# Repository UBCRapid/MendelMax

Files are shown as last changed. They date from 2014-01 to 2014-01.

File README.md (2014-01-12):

UBC Rapid
=========

MendelMax Printer
-----------------

Our newest printer, being built following the 1.5+ [MendelMax](http://mendelmax.com/tikiwiki/tiki-index.php?page=MendelMax) design.

### Current Objectives

(And feel free to add in your own)

* Sourcing parts and beginning construction.
* Printing parts (finished, except for extruder)
* Deciding on a classy name for the new member of our printer family. ("Maxwell" ?)

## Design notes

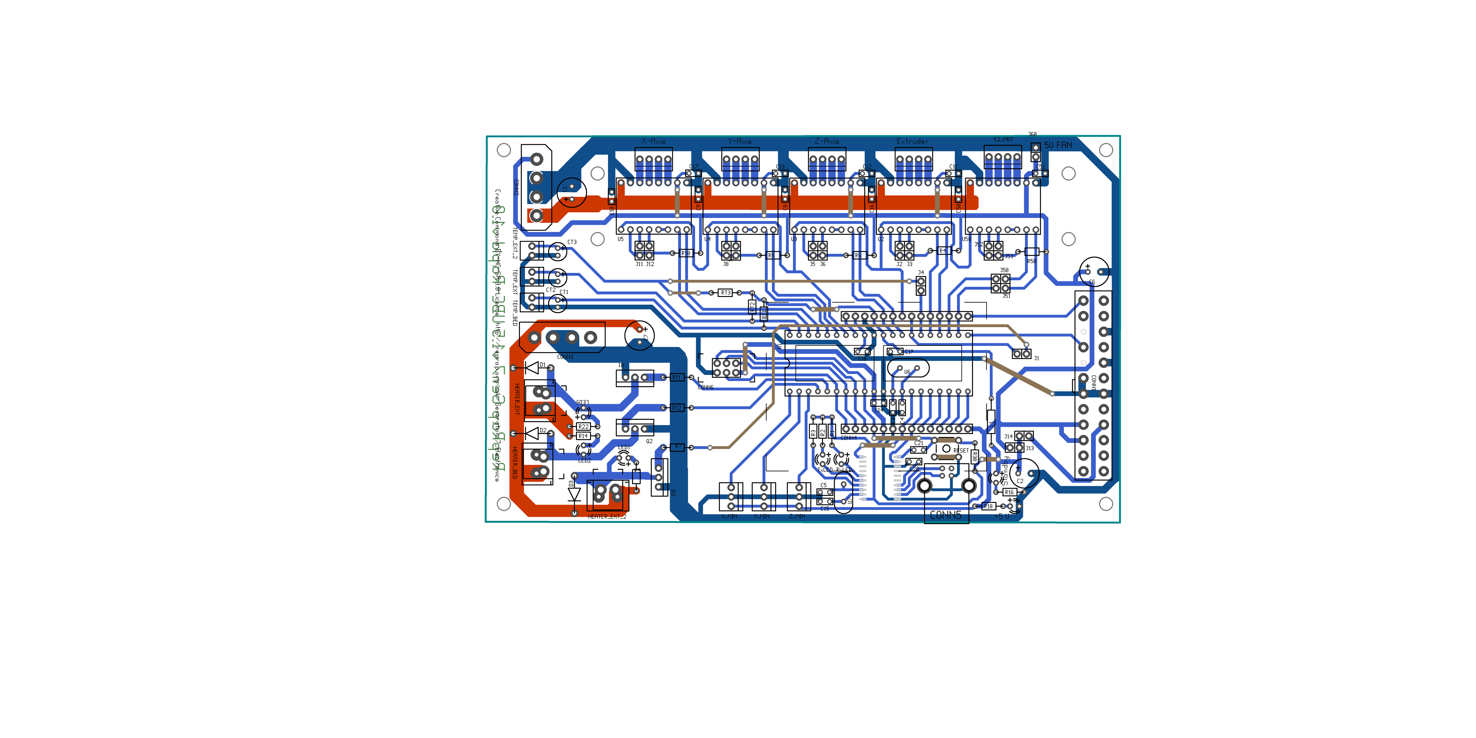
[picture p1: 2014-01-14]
Gen7Respin-Steve/Gen7Board-AVR.png

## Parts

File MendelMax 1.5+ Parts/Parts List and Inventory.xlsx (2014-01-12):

O=ordering
H=Have | MendelMax V1.5+ |  | REVISED 8/31/12 by papabur |  | MendelMax V1.5+ |  | 7/9/2012 (revised 7/9/12 by MP)
❑=not have | Full Kit Packing List |  |  |  | Hardware Kit
nn=not needed
 | Item | Qty. | Used For |  | Item | Qty. | Used For
❑ | Extrusions | 1 set |  | ❑ | Extrusions | 1 set
❑ | 420mm extrusions – Drilled | 2 | Top horizontal bars | ❑ | 420mm extrusions | 2 | Top horizontal bars
❑ | 420mm extrusions | 5 | Lower Y extrusions | ❑ | 420mm extrusions | 5 | Lower Y extrusions + Y Axis Rail Mount
❑ | 340mm Extrusions – Tapped | 4 | Diagonals | ❑ | 340mm Extrusions | 4 | Diagonals
❑ | 300mm extrusions – Tapped | 4 | Lower X extrusions | ❑ | 300mm extrusions | 4 | Lower X extrusions
❑ | Y-Axis Linear Rail and Carriage | 1 set | Y axis | ❑ | Y-Axis Linear Rail and Carriage | 1 set
❑ | Shaft Tube | 1 set |  | ❑ | Shaft Tube | 1 set
H? | M8 Precision Linear Shafting – 445mm | 2 | X axis | ❑ | M8 Precision Linear Shafting – 445mm | 2 | X axis
H? | M10 Precision Linear Shafting – 405mm | 2 | Z axis | ❑ | M10 Precision Linear Shafting – 405mm | 2 | Z axis
❑ | Leadscrews (PBC) | 2 | Z axis | ❑ | Acme Leadscrews | 2 | Z axis
❑ | Electronics | 1 set |  |  | Table Acc.
nn | LED Frame Lights | 2 | wrapped w/ table | ❑ | Borosilicate Glass Table | 1 | Print table
❑ | 24V Kapton Heater | 1 | Insulating bed heater (w/ table) | ❑ | G10 Plate | 1 | Print table lower frame
H | 24V Power Supply | 1 |  | ❑ | PET Film Bed Sheets | 2 | Optional print surface
H | Nema17 Stepper Motor | 4
H | 24V > 12V step down converter | 1 |  | ❑ | Electronics | 1 set
H | USB Cable |  |  | ❑ | LED Frame Lights (5 sections)(w/ table Acc.) | 2
 |  |  |  | ❑ | Silicone Heater (Voltage ______) | 1
❑ | RAMPS Electronics Box | 1 |  | ❑ | SSR (only with 110v or 240v beds!!!) | 1 | (AC Heaters only)
H | Arduino Mega | 1
nn | Endstop Kit | 1 |  | ❑ | Assembly tools | 1 set
H | Pololu Module | 4 |  | ❑ | 1.5mm Allen Key | 1
 |  |  |  | ❑ | 2mm Allen Key | 1
❑ | Assembly tools | 1 set |  | ❑ | 2.5mm Allen Key | 1
H | 1.5 Allen Key | 1 | ( All allen keys are in H.W. Bag) | ❑ | 3mm Allen Key | 1
H | 2mm Allen Key | 1 |  | ❑ | 3.5mm Allen Key | 1
H | 2.5mm Allen Key | 1 |  | ❑ | 4mm Allen Key | 1
H | 3mm Allen Key | 1 |  | ❑ | 6mm Allen Key | 1
H | 3.5mm Allen Key | 1
H | 4mm Allen Key | 1
H | 6mm Allen Key | 1 |  |  | Anti-Bind X axis bushings (in H.W. Bag)
H | Digital Caliper | 1 |  | ❑ | 8mm self-aligning bronze bushings | 4
H | Small Files | 1
H | Large File | 1 |  | ❑ | SSR Hardware Bag (For AC bead heaters only) | 1 set | (See bag label for contents)
H | Pololu Adjustment Tool | 1 | (w/ RAMPs Electronics Box)
H | Square | 1 |  | ❑ | Hardware Bag | 1 set | (See Bag Label for contents)
H | Zip-ties | 10 |  | ❑ | PBC Nuts(in H.W. Bag) | 2
❑ | Plastic Parts | 1 set |  | ❑ | Y Axis Rail Bag (HW bag) | 1 Set | (See Bag Label for contents)
❑ | X Idler End | 1
❑ | X Motor End | 1 |  | ❑ | Y Axis Mounting Bag (HW bag) | 1 Set | (See Bag Label for contents)
❑ | X Carriage Supaflat | 1
❑ | X Carriage Bushing Mounts | 4 |  | ❑ | Bed Thermistor Connector Bag (24V Bed Heaters only) | 1 Set | (See Bag Label for contents)
❑ | X Carriage Belt Clamps | 2
❑ | Y motor Mount | 1 |  |  | Thermistor Bag (Optional)(HW bag) | 1 set | (See Bag Label for contents)
❑ | Y Axis Belt Tensioner | 1
❑ | Y Carriage Belt Bracket | 1 |  |  | Wade's Extruder Bag (Optional)(HW Bag) | 1 set | (See Bag Label for contents)
❑ | Z Motor Mounts | 2
❑ | Z Lower Mount | 2 |  |  | make sure to include a Lead Nut Adapter bag
❑ | Z Rod Clamp | 4 |  |  | with Hardware Kit orders since these people
❑ | Spool Holder Bracket | 2 |  |  | most likely have the old style x-ends!!
❑ | Left Vertex Corner | 2
❑ | Right Vertex Corner | 2 |  |  | -T.S. revised 8/21/12
❑ | Left Vertex Cover | 2
❑ | Right Vertex Cover | 2
❑ | Upper Reinforcing Bracket | 3
❑ | RAMPs Mounting Bracket | 1
 | Table Accesories
? | Borosilicate Glass Table | 1 | Print Surface
? | G-10 Carbon Bed Sheet | 1
H | PET Film Bed Sheets | 2
❑ | Kapton Tape Roll | 1
❑ | 1LB Filament - ❑ ABS , ❑ PLA | 1
❑ | Hardware Bag | 1 set | (See bag label for contents)
 | PBC Nuts(in H.W. Bag) | 2
❑ | Wire Harness and PSU Mount Bag | 1 set | (See bag label for contents)
❑ | Micro Extruder Bag | 1 set | (See bag label for contents)
❑ | Y Axis Rail Bag (in H.W. Bag) | 1 Set | (See bag label for contents)
❑ | Y Axis Mounting Bag (in H.W. Bag) | 1 Set | (See bag label for contents)
❑ | Bed Thermistor Bag (in H.W. Bag) | 1 | (See bag label for contents)

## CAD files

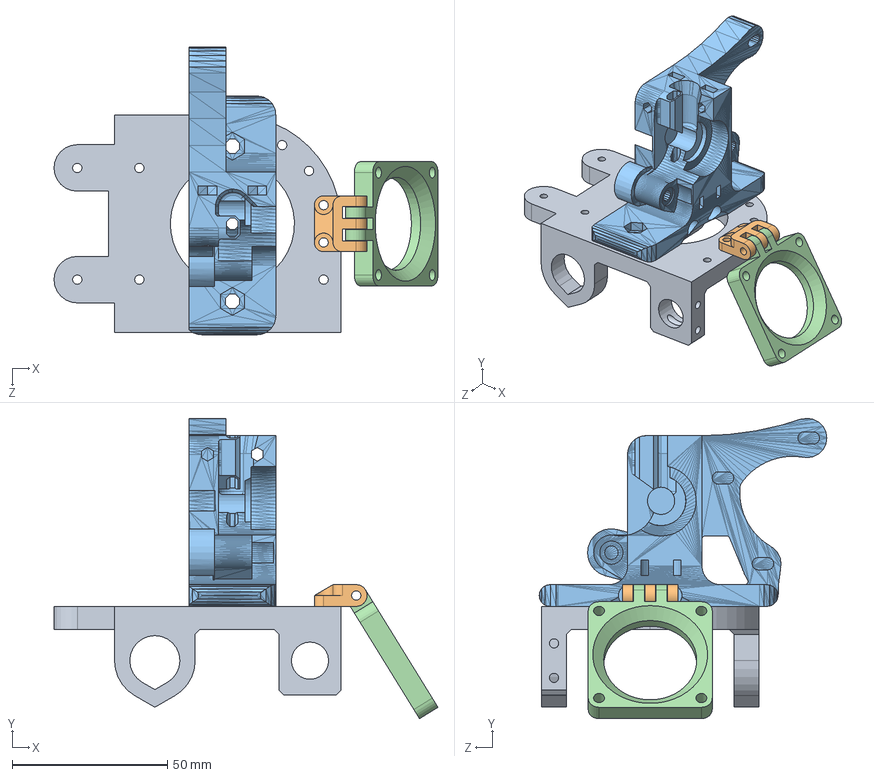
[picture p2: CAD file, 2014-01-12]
MendelMax 1.5+ Parts/Original Parts/Rough XCarriange Assembly.SLDASM
123.7 x 96.8 x 92.7 mm
Specialized X Carriage
Fan Mount 2
Toms_guided_greg
Fan Shroud

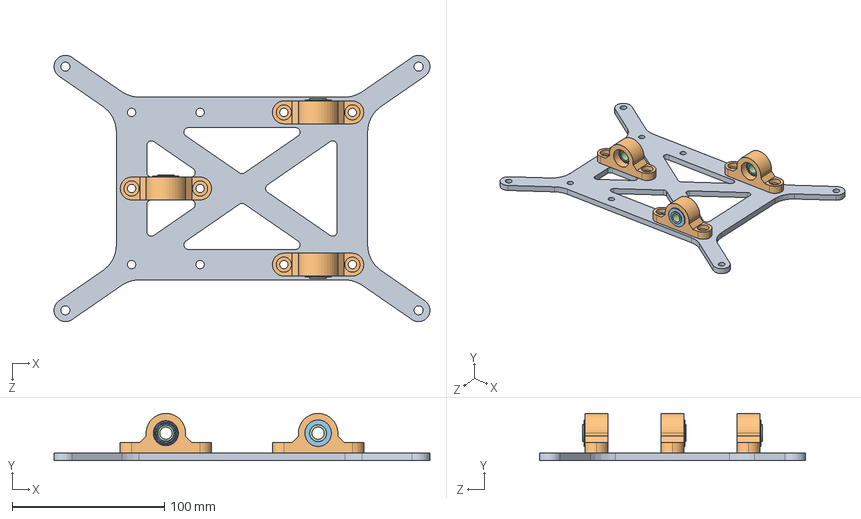
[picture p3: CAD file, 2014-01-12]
Y-Axis/Slide Plate Assembly.SLDASM
247.0 x 31.0 x 175.0 mm
Bearing Plate
Bushing Mount x 3
Bushing Holder x 3
Teflon Bushing x 3

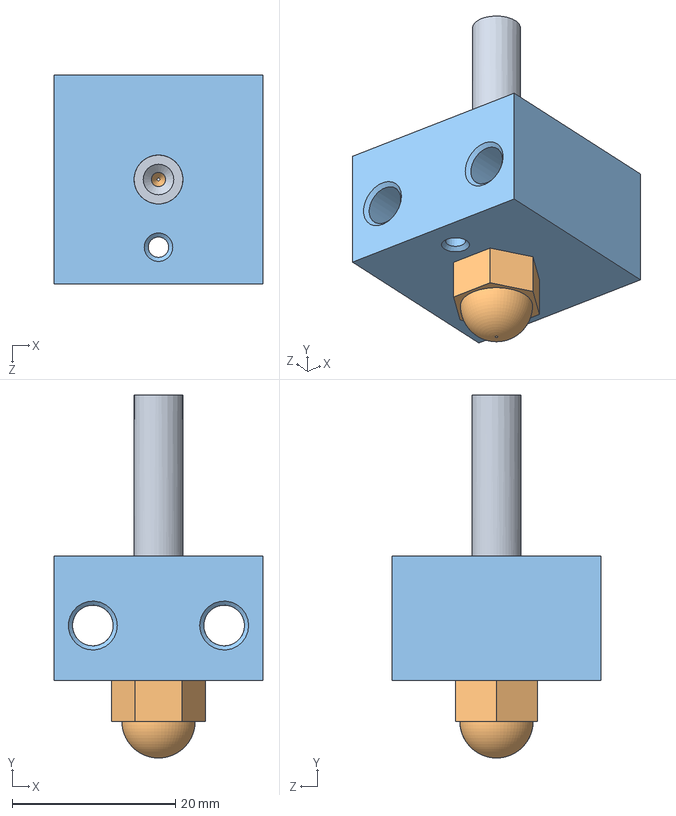
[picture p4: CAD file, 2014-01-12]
Hot End/BIQ-Based Hot End.SLDASM
25.6 x 44.5 x 25.6 mm
Brass Tube
Nozzle
Aluminum Heater Block

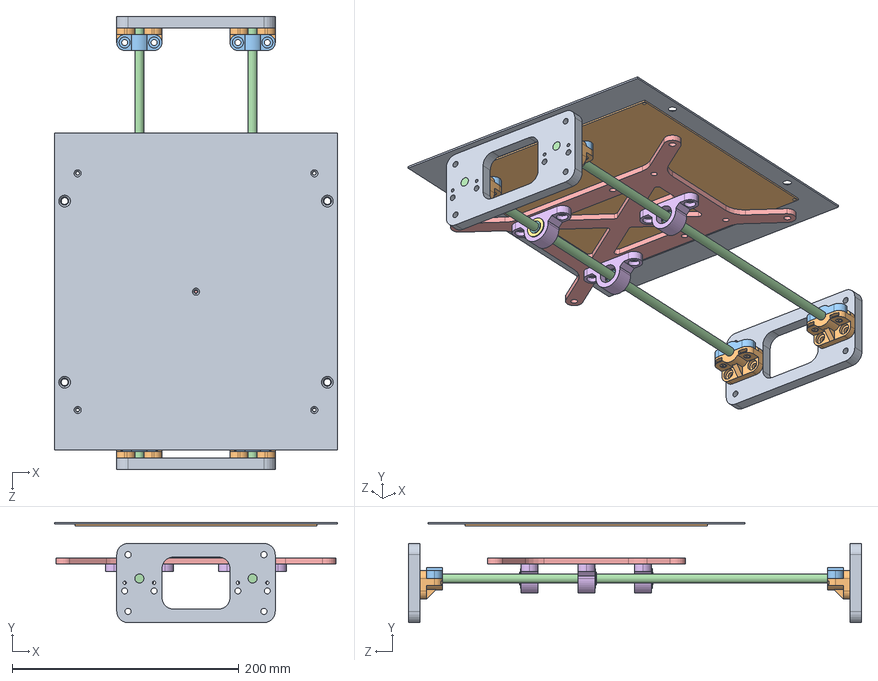
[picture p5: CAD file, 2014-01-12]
Y-Axis/Y-Axis.SLDASM
250.0 x 88.6 x 400.0 mm
Clamp Mounting Plate x 2
Rod Clamp Bracket x 4
Rod Clamp x 4
Axis Rod x 2
Bearing Plate
Bushing Mount x 3
Bushing Holder x 3
Teflon Bushing x 3
Heat Spreading Plate
Heating Plate

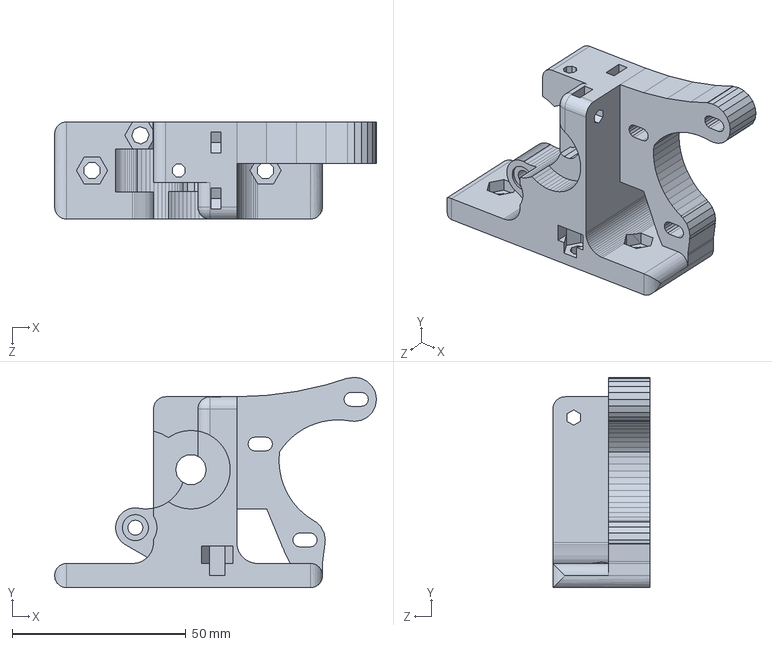
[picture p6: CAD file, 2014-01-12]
Cold End/Extruder/Modified Extruder.SLDASM
92.7 x 60.6 x 28.0 mm

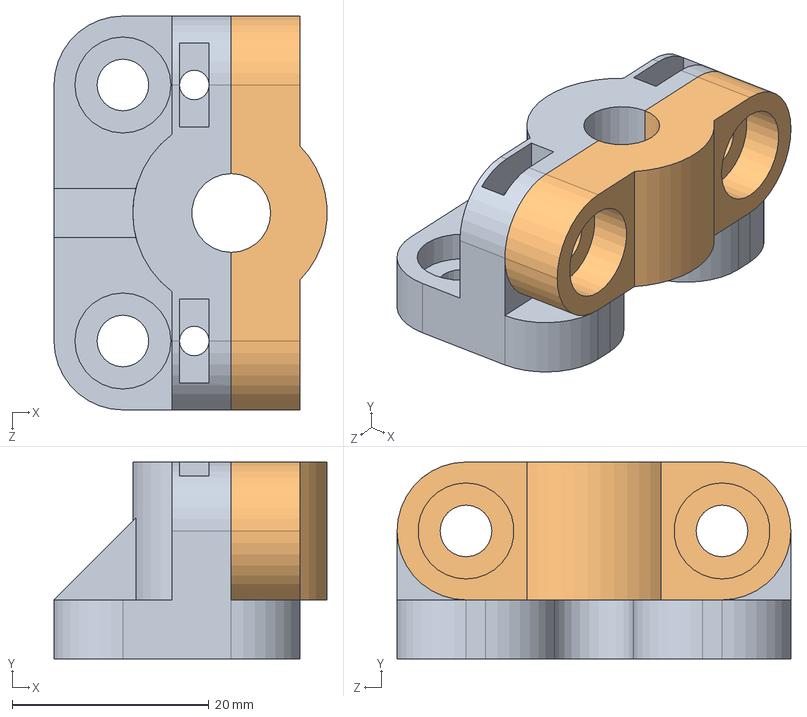
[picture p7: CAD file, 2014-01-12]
Y-Axis/Clamp Assembly.SLDASM
27.7 x 20.0 x 40.0 mm
Rod Clamp Bracket
Rod Clamp

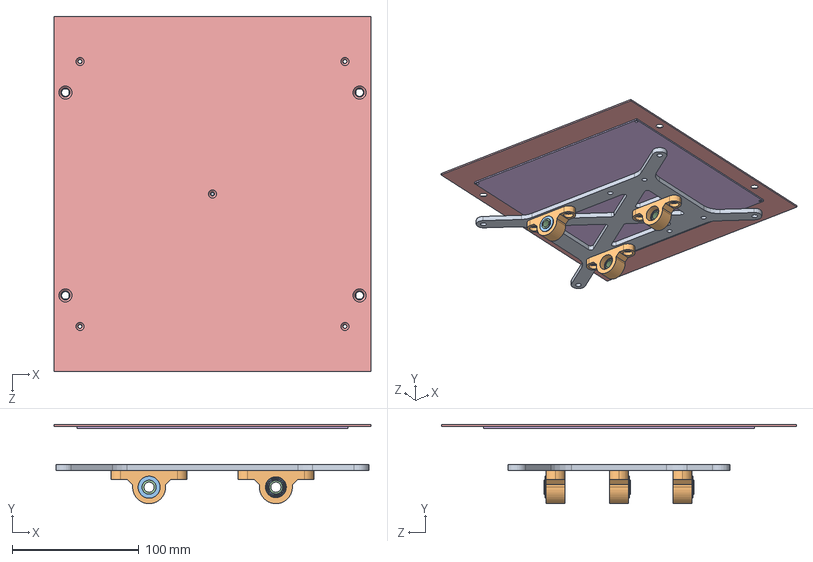
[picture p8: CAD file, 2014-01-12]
Y-Axis/Carriage Assembly.SLDASM
250.0 x 62.6 x 280.0 mm
Bearing Plate
Bushing Mount x 3
Bushing Holder x 3
Teflon Bushing x 3
Heat Spreading Plate
Heating Plate

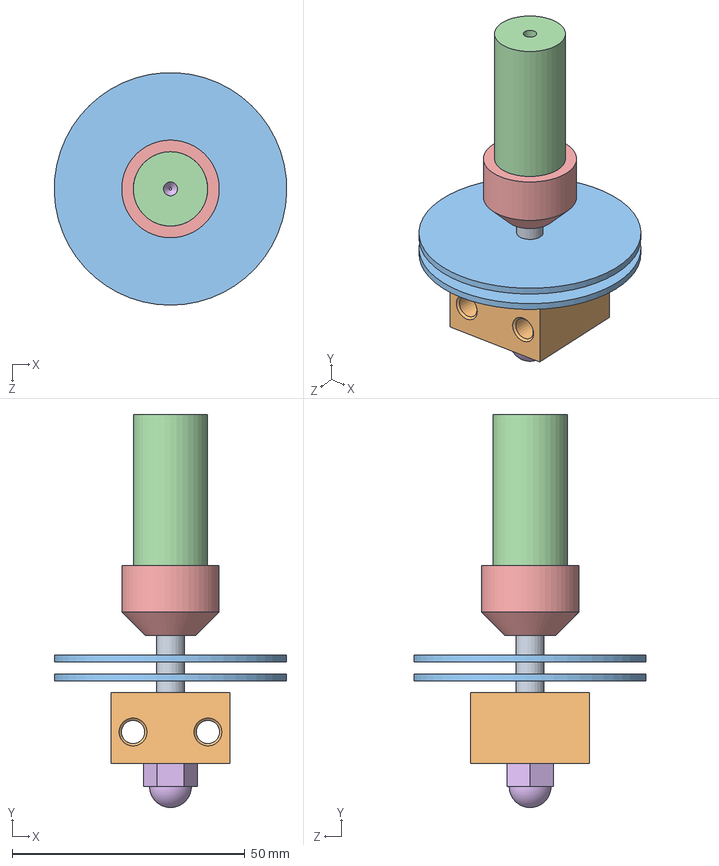
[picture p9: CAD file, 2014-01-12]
Hot End/Hot End Assembly.SLDASM
50.0 x 84.5 x 50.0 mm
Brass Tube
Aluminum Heater Block
Heat Sink Plate x 2
PTFE Cylinder
Holder PTFE
Nozzle

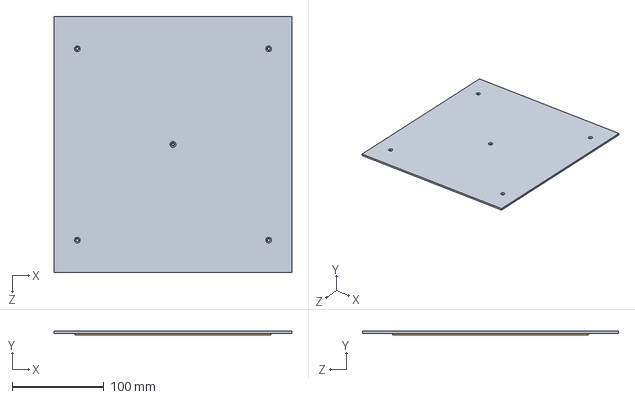
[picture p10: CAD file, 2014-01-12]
Y-Axis/Print Bed Assembly.SLDASM
260.0 x 4.10 x 280.0 mm
Heat Spreading Plate
Heating Plate

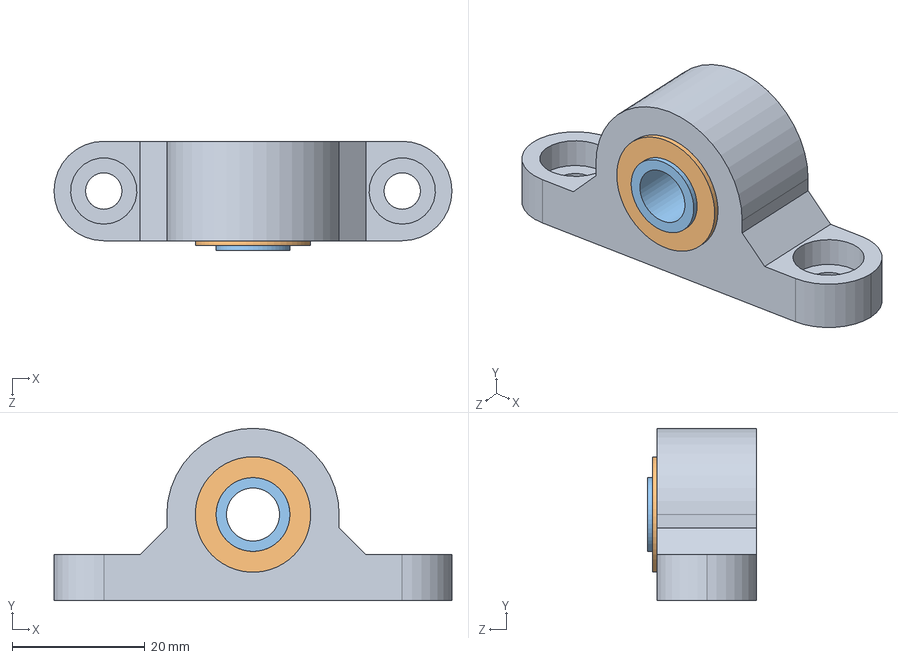
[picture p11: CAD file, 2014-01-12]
Y-Axis/Bushing Assembly.SLDASM
60.0 x 26.0 x 16.5 mm
Bushing Mount
Bushing Holder
Teflon Bushing

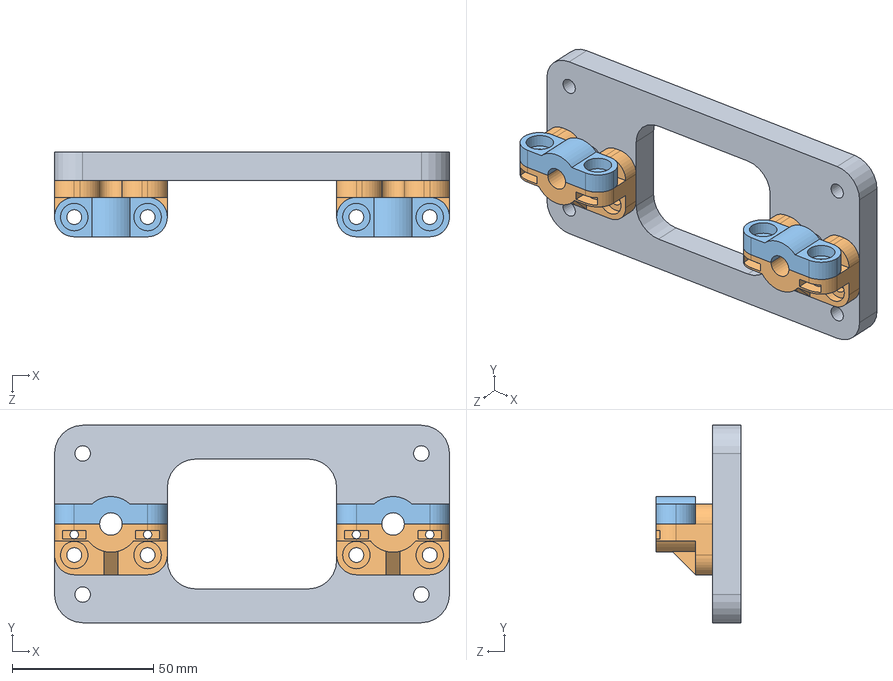
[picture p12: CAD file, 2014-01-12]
Y-Axis/Axis Clamp.SLDASM
140.0 x 70.0 x 30.0 mm
Clamp Mounting Plate
Rod Clamp Bracket x 2
Rod Clamp x 2

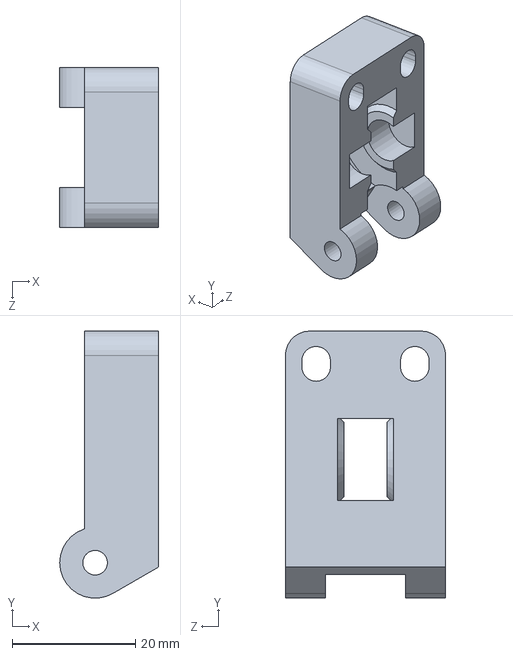
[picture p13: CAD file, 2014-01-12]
Cold End/Extruder/Idler.SLDPRT
16.0 x 43.3 x 26.0 mm

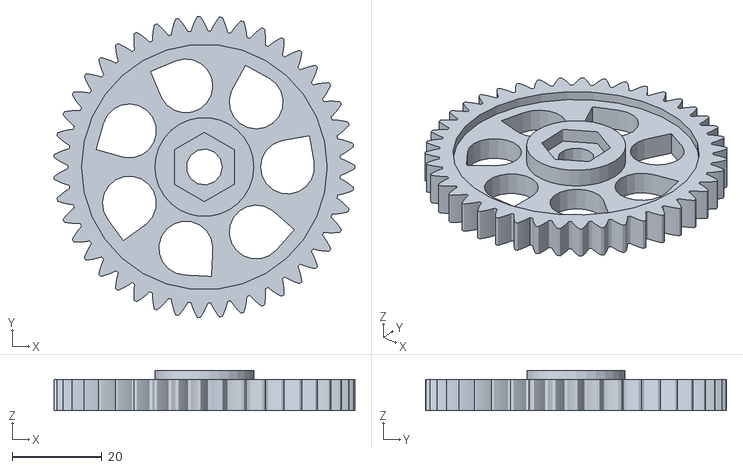
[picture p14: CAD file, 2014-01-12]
Cold End/large_gear.stl
66.9 x 67.0 x 9.00

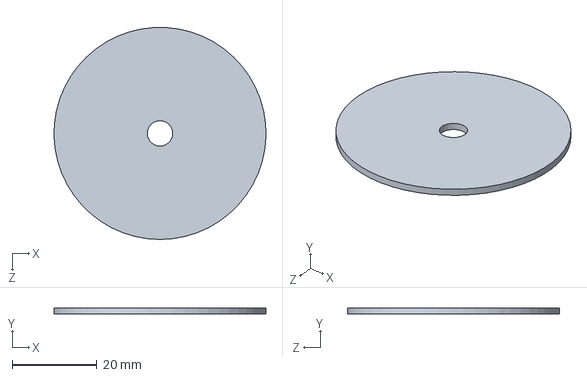
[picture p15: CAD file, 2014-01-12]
Hot End/Heat Sink Plate.SLDPRT
50.0 x 1.50 x 50.0 mm

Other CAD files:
MendelMax 1.5+ Parts/Community Parts/Z Motor-Rod Coupling.stl
Cold End/Extruder/NEMA 17 Stepper Motor.SLDPRT
Cold End/Toms_guided_greg_v3.stl
Hot End/Nozzle.SLDPRT
Cold End/Extruder/608RS Bearing.SLDPRT
Cold End/Extruder/Mount.SLDPRT
Cold End/Extruder/STLIdler.SLDPRT
Cold End/Toms_guided_greg.SLDPRT
Cold End/idler.stl
Cold End/small_gear.stl
Hot End/Aluminum Heater Block.SLDPRT
Hot End/Brass Tube.SLDPRT
Hot End/Holder PTFE.sldprt
Hot End/PTFE Cylinder.SLDPRT
MendelMax 1.5+ Parts/Community Parts/X Carriage.stl
MendelMax 1.5+ Parts/Original Parts/Belt Clamp.SLDPRT
MendelMax 1.5+ Parts/Original Parts/Endstop Rod Mount.SLDPRT
MendelMax 1.5+ Parts/Original Parts/Fan Mount.SLDPRT
MendelMax 1.5+ Parts/Original Parts/Fan Shroud.SLDPRT
MendelMax 1.5+ Parts/Original Parts/Mirrored Spool Bearing Holder.SLDPRT
MendelMax 1.5+ Parts/Original Parts/Modified X Carriage.SLDPRT
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

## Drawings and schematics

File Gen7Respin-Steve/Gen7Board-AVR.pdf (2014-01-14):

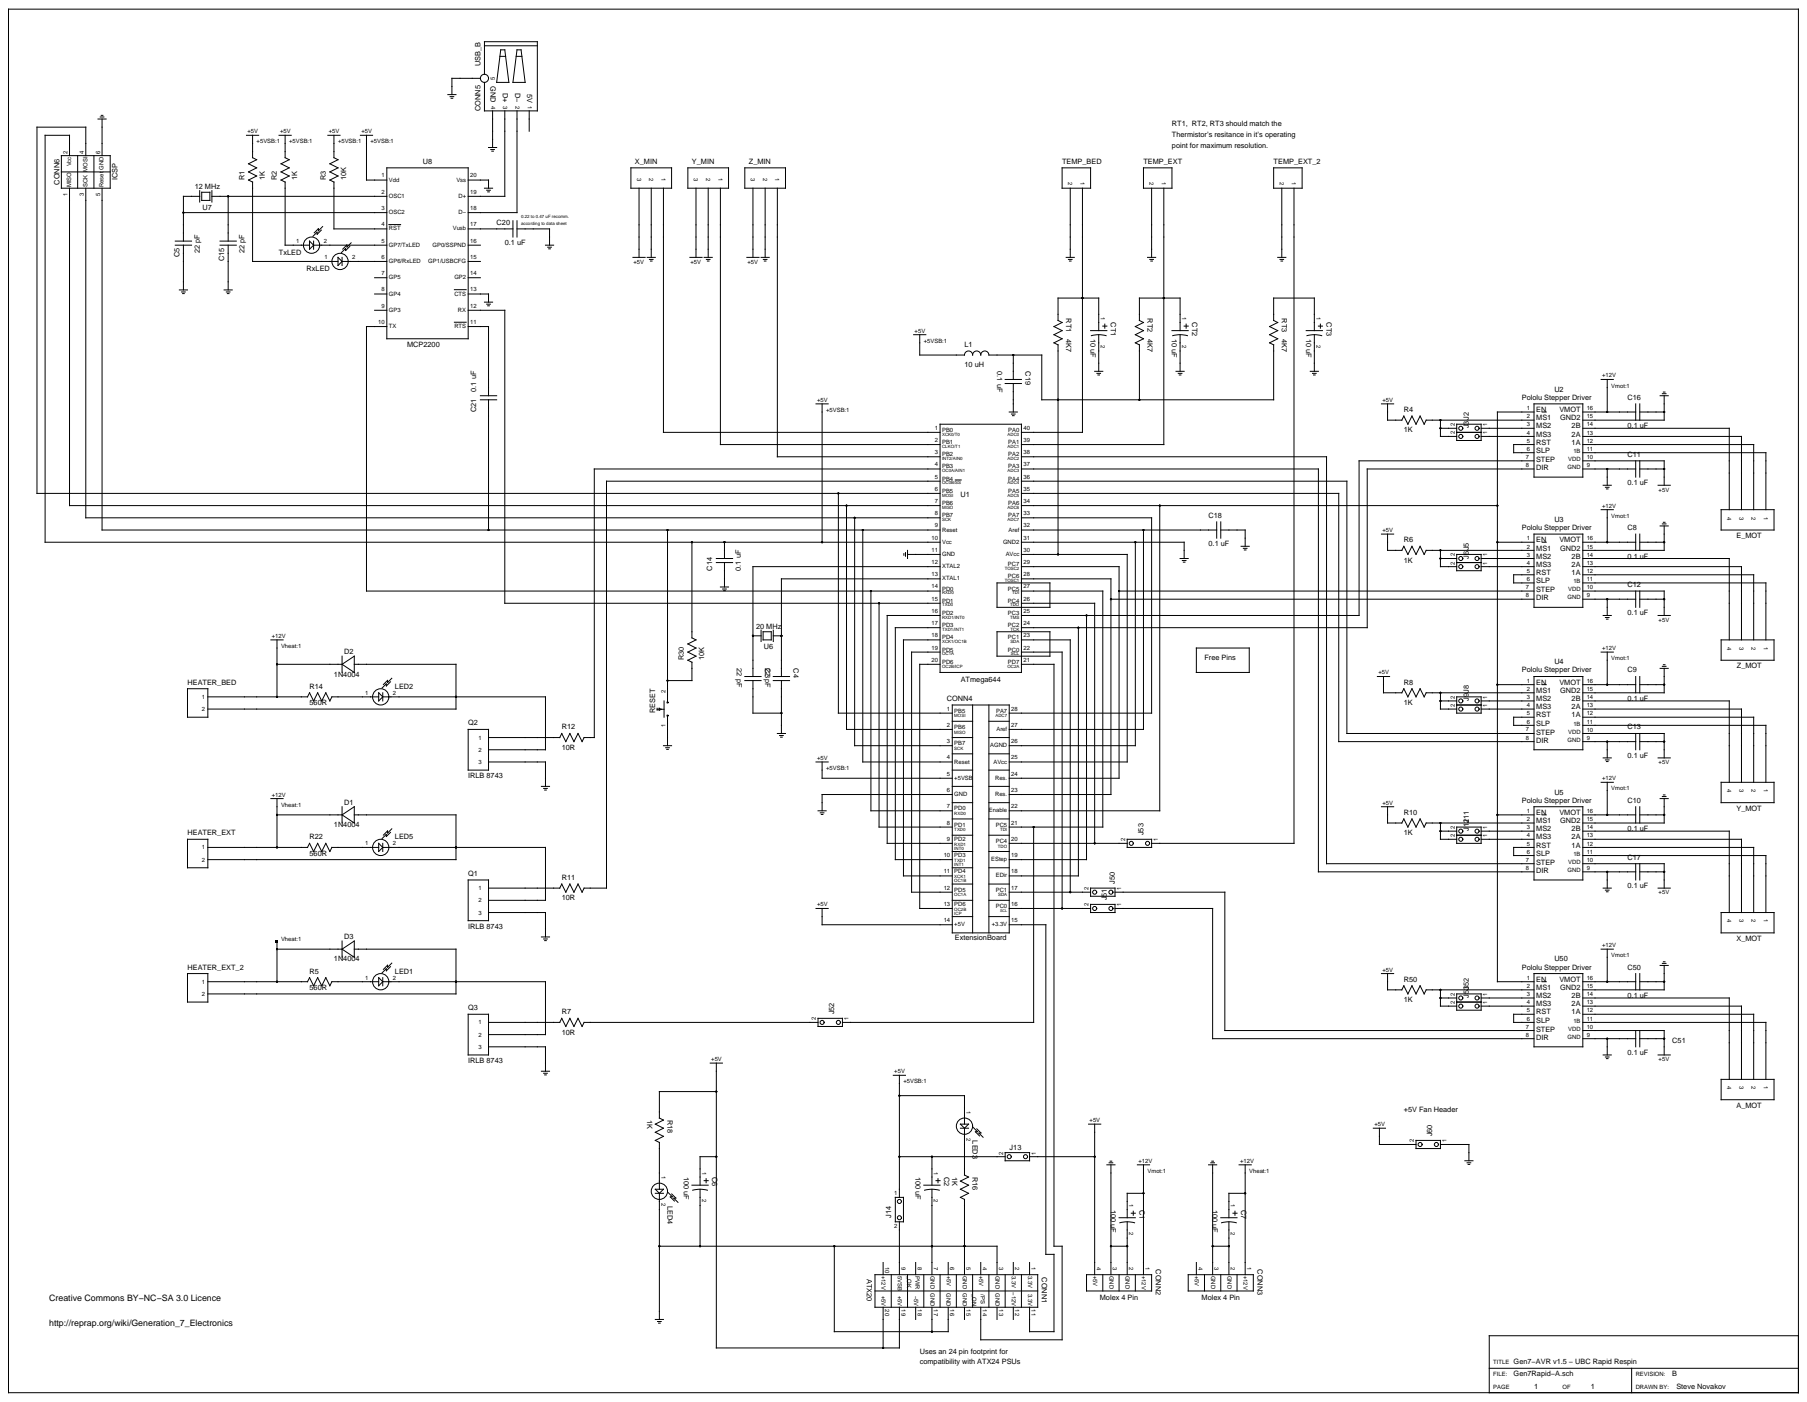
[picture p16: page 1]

RT1, RT2, RT3 should match the
Thermistor’s resitance in it’s operating
point for maximum resolution.

according to data sheet

PB5 1 MOSI | ADC7

PB6 2 MISO | Aref

Reset 4 | AVcc

+5VSB 5 | Res.

GND 6 | Res.

PD0 7 RXD0 | Enable

PD1 8 TXD0 | PC5 TDI

PD2 RXD1 INT0 | PC4 TDO

PD3 TXD1 INT1 | EStep

PD5 12 OC1A | PC1 SDA

PD6 OC2B ICP | PC0 SCL

CONN3 Creative Commons BY−NC−SA 3.0 Licence Molex 4 Pin

http://reprap.org/wiki/Generation_7_Electronics

Uses an 24 pin footprint for
compatibility with ATX24 PSUs

Gen7−AVR v1.5 − UBC Rapid Respin
TITLE
Gen7Rapid−A.sch

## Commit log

2012-10-12 Initial Commit
    Added parts list and .stl files for the printable parts. Readme, etc.
    [Lower Vertex Lower_Left_2_copies.stl, Lower Vertex Lower_Right_2_copies.stl, Lower Vertex Upper_left_2_copies.stl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]
2012-11-26 Top Vertex Models
    Added Solidworks model and DXF drawings of the Top Vertex, contains two
    configs (with and without the UBC Rapid Logo).
    [Top Vertex (Default).DXF, Top Vertex (Logo).DXF, Top Vertex SLDPRT.SLDPRT]
2012-11-27 Extruder Files added
    Files for Tom's guided Greg's accesable extruder added, README updated.
    [Toms_guided_greg.SLDPRT, Toms_guided_greg_v3.stl, idler.stl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]
2012-12-11 Initial (sloppy) hot end modelling
    [Aluminum Heater Block.SLDPRT, Brass Tube.SLDPRT, Heat Sink Plate.SLDPRT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]
2012-12-14 Hot-End and Y-Axis Added
    [Axis Mounting Plate.SLDPRT, BIQ-Based Hot End.SLDASM, Brass Tube.SLDPRT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]
2013-01-05 More Y-Axis Changes
    [608RS Bearing.SLDPRT, Axis Clamp.SLDASM, Axis Mounting Plate.SLDPRT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]
2013-01-05 Ditto (y-axis changes)
    [Clamp Mounting Plate.SLDPRT]
2013-01-08 Rotated Y-Rod Clamp
    [Axis Clamp.SLDASM, Axis Rod.sldprt, Bushing Assembly.SLDASM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]
2013-01-13 Y-Axis Heating Plate, Bearing Mount changes
    [Bearing Plate.SLDPRT, Bushing Assembly.SLDASM, Bushing Mount STL.STL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]
2013-01-15 X Axis Clamp Change
    [X Axis Clamp.SLDPRT, X End Clamp MOD for MendelMax Leadscrew_1_copy.STL]
2013-01-19 Y-motor mount Solidworks
    [Y-axis Motor Mount.SLDPRT]
2013-01-20 Changes to Y-Axis Assembly, Nut Bracket
    [Bearing Plate.SLDPRT, Carriage Assembly.SLDASM, Heat Spreading Plate.SLDPRT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]
2013-03-02 Created solidworks models for most of the parts
    [Bearing Plate.SLDPRT, Belt Clamp.SLDPRT, Carriage Assembly.SLDASM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]
2013-03-04 Added X End Models
    [X End Clamp MOD for MendelMax Leadscrew_1_copy.STL, X End Idler.SLDPRT, X End Motor Mount.SLDPRT]
2013-03-09 Endstop and Z Top Vertex
    [Endstop Rod Mount.SLDPRT, Z Top Vertex.SLDPRT]
2013-04-16 Initial Custom Fan Mount Commit
    [Fan Mount.SLDPRT]
2013-04-16 Branched XCarriage, Added Fan Mount for it
    [Fan Mount 2.SLDPRT, Modified X Carriage.SLDPRT, Specialized X Carriage.SLDPRT]
2013-05-02 Added carriage, fan shroud, and spool mounts
    [Fan Mount 2.SLDPRT, Fan Mount 2.STL, Fan Mount 3.STL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]
2013-05-05 Final changes to Xcarriage and fan stuff
    [Fan Mount 2.SLDPRT, Fan Mount 2.STL, Fan Mount 3.STL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]
2013-05-09 Added mirror of bearing holder
    [Mirrored Spool Bearing Holder.SLDPRT]
2014-01-08 Steve Adding Gen 7 Respin
    [ExtensionBoard-USB-B.sch, Gen7Board-AVR.sch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]
2014-01-12 Fixed MOSFET resistor issue
    [Gen7Board-AVR.sch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]
2014-01-12 Fixing MOSFET resistor issue on gen7 respin
    [608RS Bearing.SLDPRT, Aluminum Heater Block.SLDPRT, Axis Clamp.SLDASM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]
2014-01-12 MOSFET Resistor fix
    [ExtensionBoard-USB-B.sch, Gen7Board-AVR.sch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]
2014-01-14 Whoops, wrong files
    [Gen7Board-AVR.sch]
